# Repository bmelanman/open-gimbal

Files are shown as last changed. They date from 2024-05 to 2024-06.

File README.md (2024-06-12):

# OpenGimbal

Now introducing: OpenGimbal - An open-source gimbal implementation utilizing the PX4-Autopilot library.

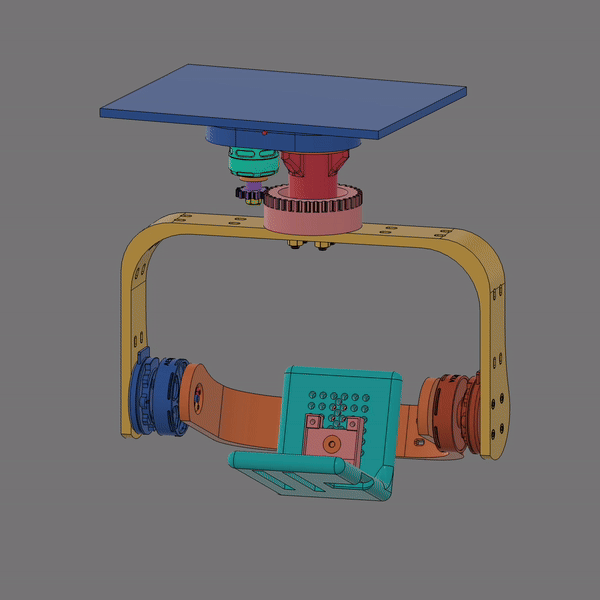
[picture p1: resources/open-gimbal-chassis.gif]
gimbal_gif


## Reference Design

This design is based on the the [OpenSAM](https://opensamofficial.github.io/OpenSAM/) 3-axis handheld camera gimbal. The slipring components have been adapted from the [Continuous Rotation Lidar Module](https://www.thingiverse.com/thing:1778878).

The gimbal uses two Vertiq 28-06 motor modules to drive the roll and yaw axes, and two* Vertiq 40-06 motor modules to drive the pitch axis. The motors are controlled by an [ARK CANnode](https://arkelectron.com/product/ark-cannode/) module running the PX4-Autopilot  OpenGimbal firmware. Additionally, a [generic 12-wire slipring](https://www.amazon.com/Taidacent-Wires12-Collector-Electrical-Connector/dp/B07NSPHVTN) is used to allow infinite range in the yaw axis.

_*Two motors were used to decrease each motor's load and heat dissipation, however a single motor may suffice depending on the use case and payload weight._

The design files, as well as any necessary hardware for assembling the gimbal, can be found in the [reference design folder][_ref_design_path] of this repository.

### Assembly Notes

Should you choose to print and assemble the provided reference design, keep in mind:

- The hardware used in the design was simply what I already had on hand at the time. The design can be easily modified to accommodate different hardware, so I would highly recommend first trying to incorporate any hardware you already have before purchasing any new parts.

- I highly recommend printing the parts in PETG with a fairly high infill, as the parts need to be quite strong to support the heat and force imparted by the motors (especially on the pitch axis).

## To Do

* [ ] Enable control over DroneCAN
* [ ] Enable axis range limits
* [ ] Add landing detection
* [ ] Tune rate controller PID values for each axis
* [ ] Add optional telemetry collection
* [ ] Add parameters to the reference design to allow for the use of different motors, sliprings, controllers, etc.
* [ ] "Spruce things up"

## Acknowledgements

* This project was sponsored largely by Alex from [ARK Electronics](https://arkelectron.com/), who provided the ARK CANnode module, the Vertiq motors, and a lot of guidance and support throughout the project. Massive thanks to him for making this project possible!

* This project is based on the work of [PX4-Autopilot](https://github.com/PX4/PX4-Autopilot), an open source flight control software for drones and other unmanned vehicles, providing a flexible set of tools for drone developers to share technologies to create tailored solutions for drone applications.

* The gimbal design is based on the [OpenSAM](https://opensamofficial.github.io/OpenSAM/) 3-axis handheld camera gimbal. 

* The slipring components have been adapted from the [Continuous Rotation Lidar Module](https://www.thingiverse.com/thing:1778878).

[_ref_design_path]: resources/reference_design
[_gimbal_gif_path]: resources/open-gimbal-chassis.gif

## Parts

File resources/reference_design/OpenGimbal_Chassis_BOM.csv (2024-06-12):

OpenGimbal Chassis BOM
Group | Part Name | Reference | Description | Quantity | McMaster-Carr Part Number | Notes
1 | Chassis Mount | chassis_mount |  | 1
1.1 | Chassis Mount Core Pin |  | Any 2.5mm dimeter rod will do | 1 | 98378A161
2 | Yaw Mount | yaw_mount |  | 1
2.1 | Yaw Motor Screws |  | Socket Head Screw, M3x0.5mm Thread, 8mm len | 4 | 91274A103
2.2 | Yaw Drive Motor |  | Vertiq 23-06 Motor Module | 1
2.2.1 | Prop Adapter |  | Vertiq 23-06 Motor Module M5 Prop Adapter | 1 |  | Included with the 23-06 motors
2.2.2 | Yaw Pinion | yaw_pinion |  | 1
2.2.3 | Prop Adapter Locknut |  | M5x0.8mm Flared Locknut | 1 |  | Included with the 23-06 motors
2.3 | Slipring |  | Generic 12 Wire Slipring | 1
2.3.1 | Slipring Screws |  | M3x0.5mm Thread, 25mm len | 3 | 92095A186
2.3.2 | Slipring Nuts |  | 4.5mm Hex, M3x0.5mm Thread, 5mm len | 3 | 94868A717 | Can be of any length, as long as it doesn't interfere with anything
2.4 | Pivot Nut |  | M8x1.25mm Thread | 1 | 90593A007
2.5 | Pivot Bearing Washer |  | M8 Screw Size, 8.2 mm ID, 11.9 mm OD | 1 | 97725A700 | Can be any M8 washer, as long as it doesn't interfere with the bearing
2.6 | Pivot Bearing |  | 608 Ball Bearing | 1 | 5972K91
2.7 | Pivot Body | pivot_body |  | 1
2.8 | Yaw Gear | yaw_gear |  | 1
2.8.1 | Yaw Gear Bolts |  | M5 x 0.8mm Thread, 16mm Long | 4 | 92000A326
3 | Upper Bracket (Yaw-Pitch) | bracket_U_top |  | 1
3.1 | Yaw Gear Nuts |  | M5 x 0.8 mm Thread | 4 | 91828A241
3.2 | Pivot Bolt Spacer | yaw_bolt_spacer |  | 1
3.3 | Pivot Bolt |  | M8 x 1.25 mm Thread, 40 mm Long | 1 | 93235A356 | Hole ID will likely need to be increased to route all wires through the bolt (~4mm in my case)
3.4 | Pitch Drive Motor(s) |  | Vertiq 40-06 Motor Module | 2 |  | A single motor should be sufficient, but a plastic spacer and bearing will need to replace it
3.4.1 | Outer Pitch Motor Screws |  | M3x0.5mm Socket Head Screw - 8mm | 8 | 91274A103
3.4.2 | Inner Pitch Motor Screws |  | M3x0.5mm Button Head Hex Screw | 8 | 92095A179
4 | Lower Bracket (Pitch-Roll) | bracket_U_bottom |  | 1
4.1 | Roll Drive Motor |  | Vertiq 23-06 Motor Module | 1
4.1.1 | Outer Roll Motor Screws |  | M3x0.5mm Socket Head Screw - 8mm | 4 | 91274A103
4.1.2 | Inner Roll Motor Screws |  | M2x0.4mm Socket Head Screw - 5mm | 4 | 91290A012
4.2 | Payload Plate | payload_plate |  | 1
4.3 | PCB Mount | pcb_mount |  | 1
4.3.1 | PCM Mount Screw |  | 10-32 Hex Drive Flat Head Screw - 9/16” | 1 | 91253A267
4.4 | PCB Cover | pcb_cover |  | 1
4.4.1 | PCB Cover Screws |  | M3x0.5mm Socket Head Screw - 8mm | 4 | 91274A103

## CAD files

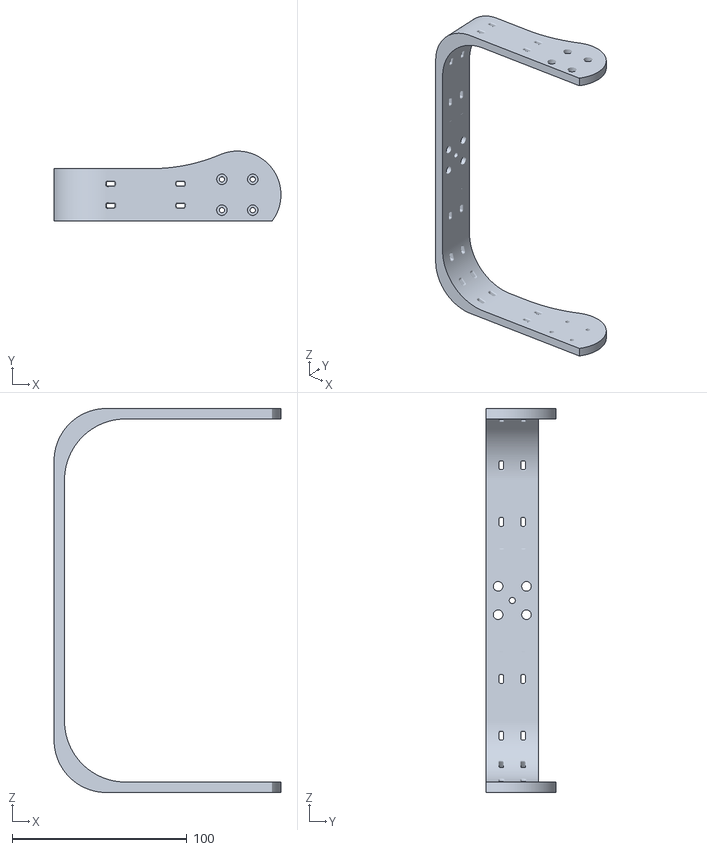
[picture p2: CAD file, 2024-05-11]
resources/reference_design/OG_bracket_U_top.stl
130.0 x 40.0 x 220.0

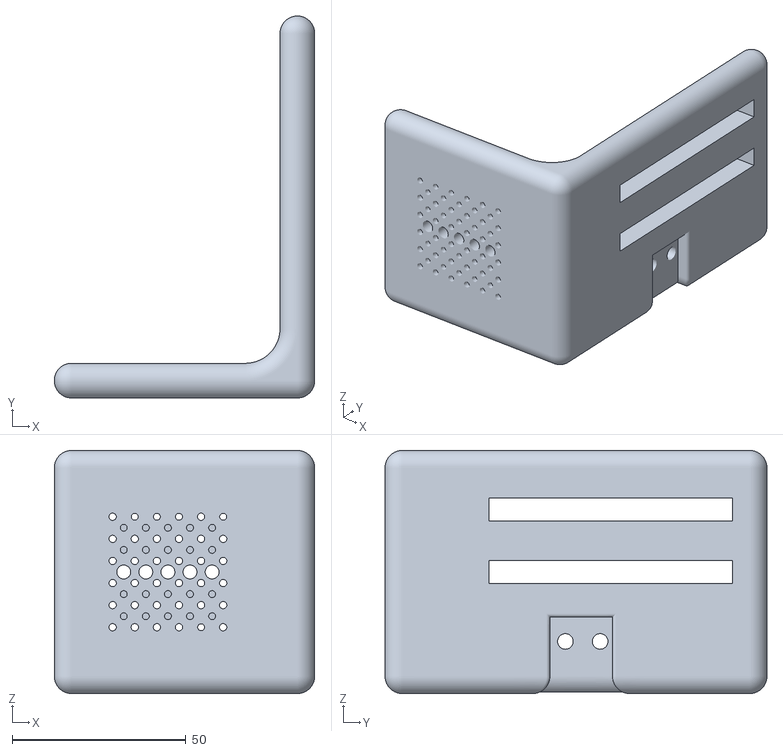
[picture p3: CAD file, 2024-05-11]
resources/reference_design/OG_payload_plate.stl
75.0 x 110.0 x 70.0

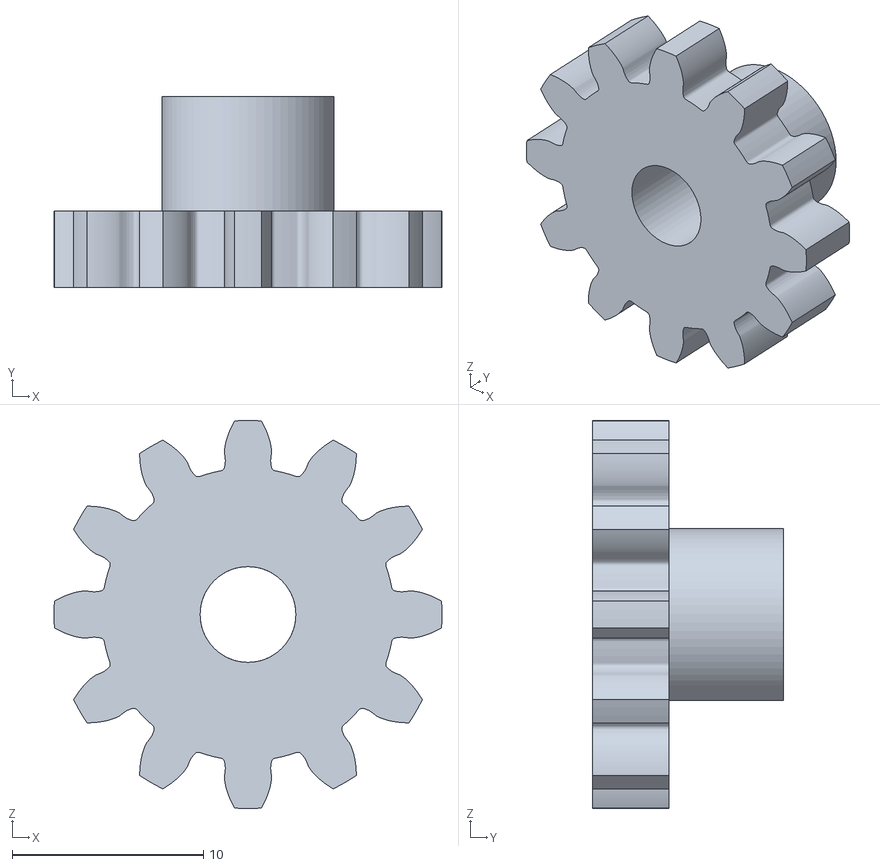
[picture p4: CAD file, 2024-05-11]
resources/reference_design/OG_yaw_pinion.stl
20.3 x 10.00 x 20.3

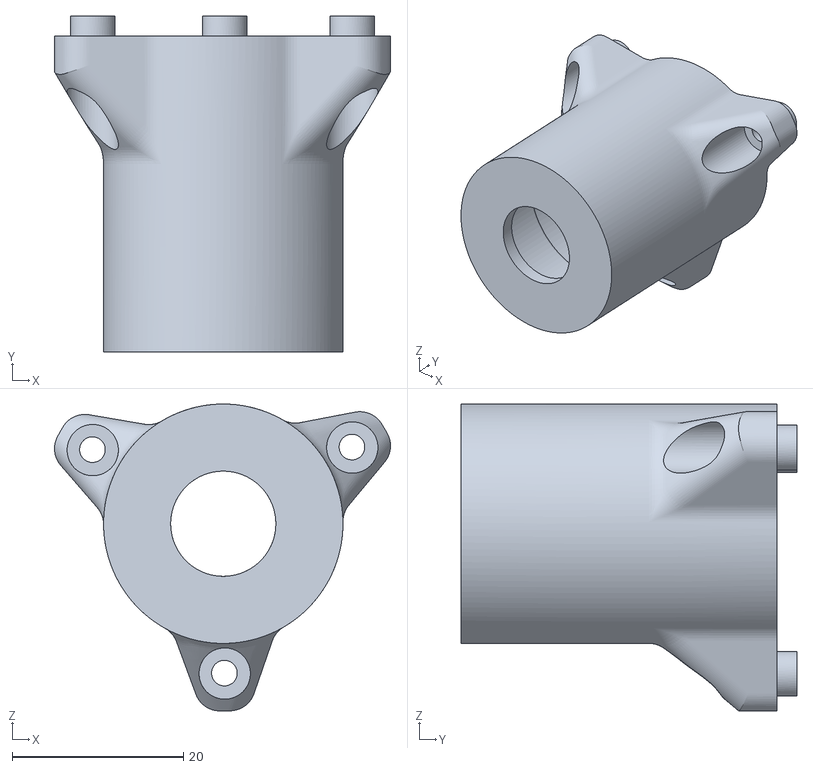
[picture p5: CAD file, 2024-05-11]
resources/reference_design/OG_pivot_body.stl
39.3 x 39.3 x 35.9

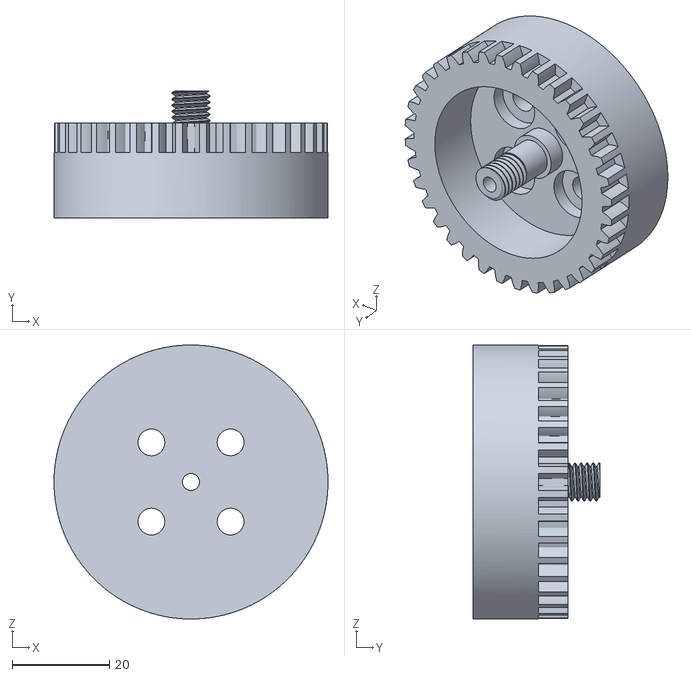
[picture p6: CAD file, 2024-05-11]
resources/reference_design/OG_yaw_gear.stl
56.3 x 26.0 x 56.3

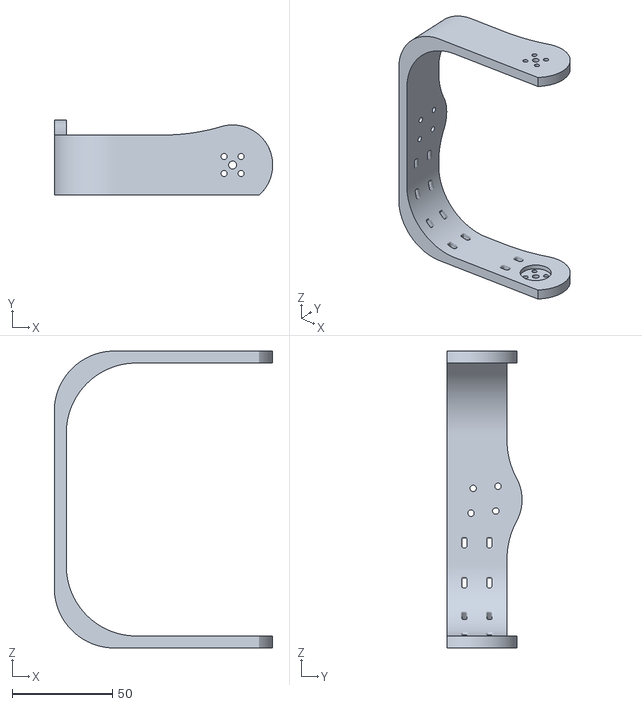
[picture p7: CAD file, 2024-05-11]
resources/reference_design/OG_bracket_U_bottom.stl
109.0 x 37.5 x 148.2

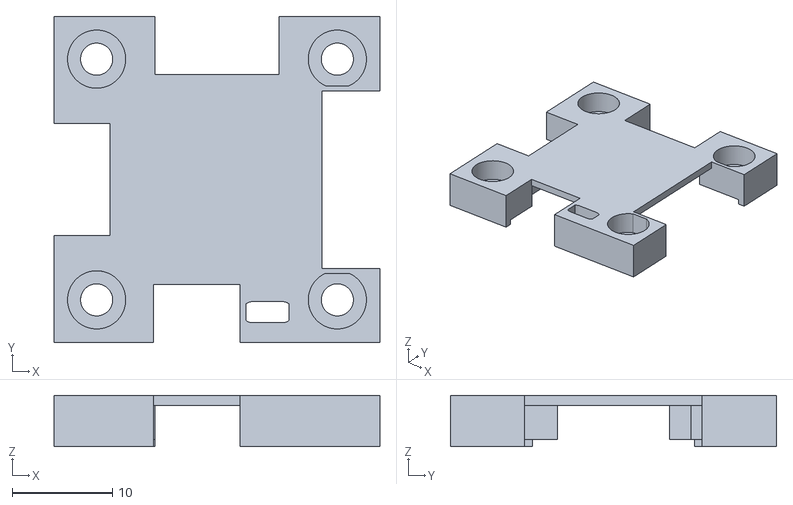
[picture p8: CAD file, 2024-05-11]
resources/reference_design/OG_pcb_cover.stl
32.5 x 32.5 x 5.10

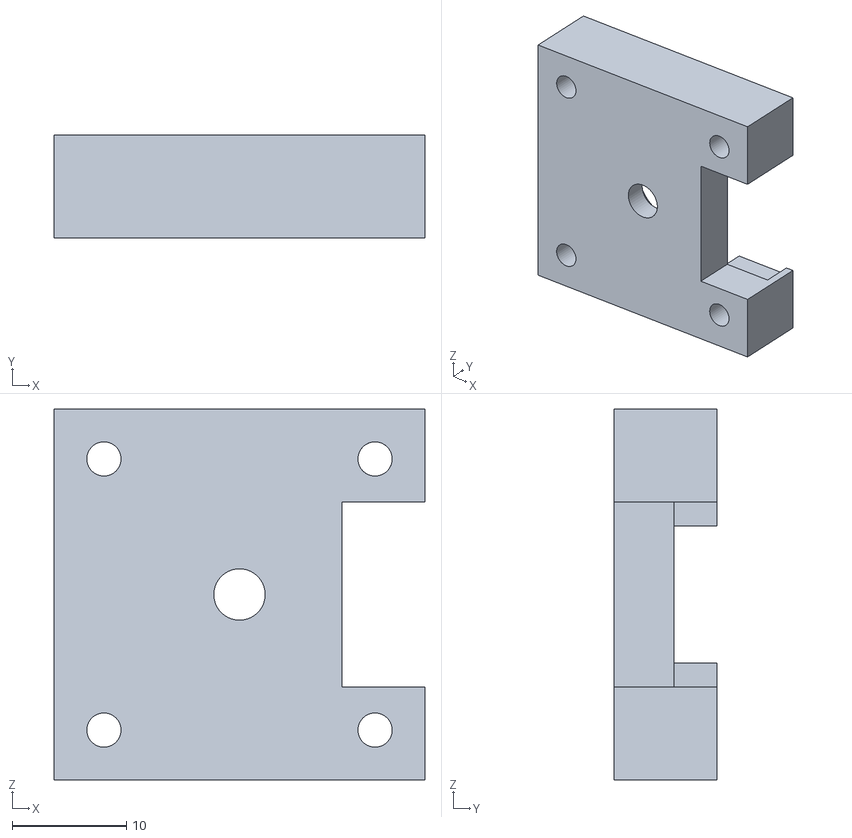
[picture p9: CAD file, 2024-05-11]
resources/reference_design/OG_pcb_mount.stl
32.5 x 9.00 x 32.5

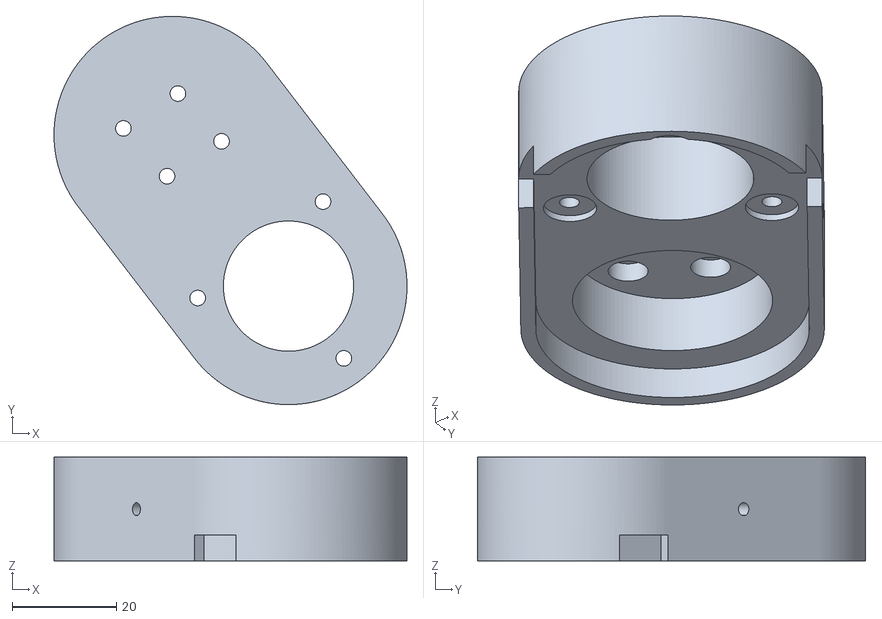
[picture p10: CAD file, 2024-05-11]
resources/reference_design/OG_yaw_mount.stl
67.8 x 74.5 x 20.0

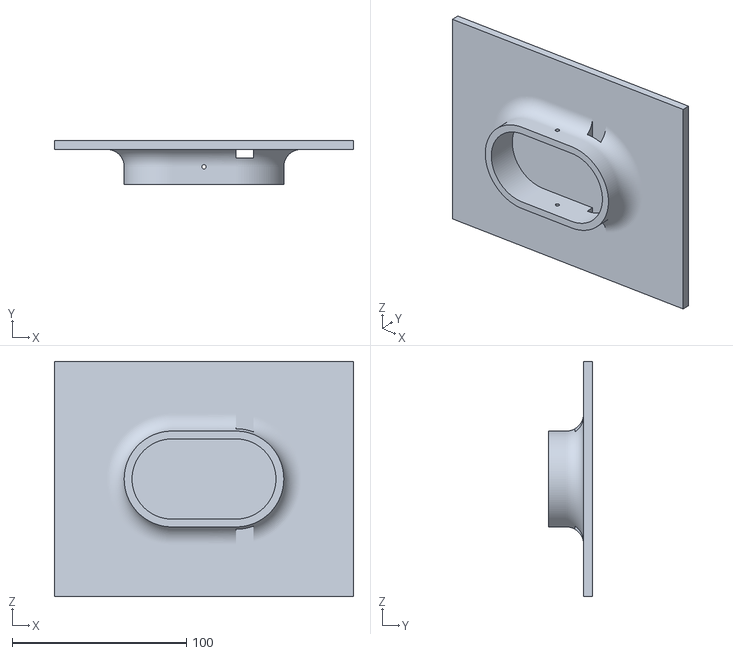
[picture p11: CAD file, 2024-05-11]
resources/reference_design/OG_chassis_mount.stl
171.6 x 25.0 x 135.0

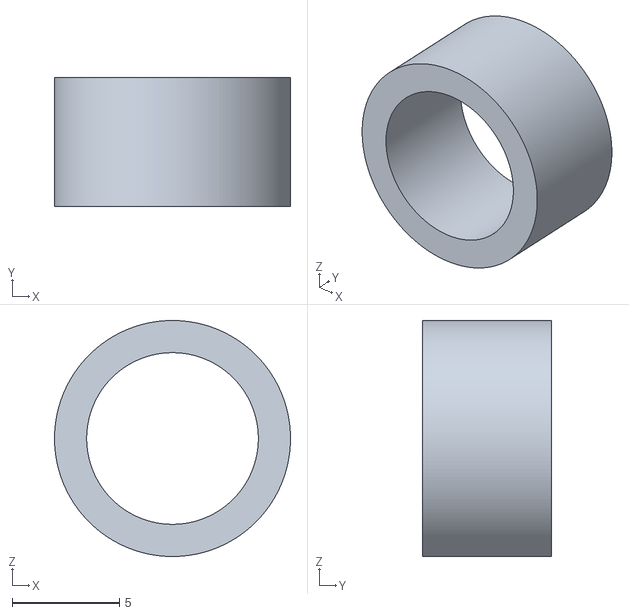
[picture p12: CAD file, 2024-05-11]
resources/reference_design/OG_yaw_bolt_spacer.stl
11.0 x 6.00 x 11.0

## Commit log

2024-05-11 Updated README to add new info and reference design files
    [OG_bracket_U_bottom.stl, OG_bracket_U_top.stl, OG_chassis_mount.stl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]
2024-06-12 Renamed `ezgif-2-9b316f240c.gif` to `open-gimbal-chassis.gif`
2024-06-12 Did some touchups on formatting and wordings
    [OpenGimbal_Chassis_BOM.csv]
